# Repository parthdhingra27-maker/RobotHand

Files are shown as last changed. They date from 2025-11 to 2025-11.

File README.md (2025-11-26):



<h1 align="center">UtiliHand: A Custom Open-Source Robotic Hand</h1>
<p align="center">Project Files:</p>

<p align="center">
  <a href="https://cad.onshape.com/documents/7d4782fc1d2b81b2411dc364/w/61aa74bc50ffa663fe78e913/e/d61dc358418eba5ccd3d28ce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">Onshape CAD Files</a> •
  <a href="https://docs.google.com/spreadsheets/d/1jZwi7d67DiPdZLEvy5LfeC6HyOPPZ9pO3xaRMX1j6oo/edit?usp=sharing">Bill of Materials</a> •
  <a href="https://blueprint.hackclub.com/projects/599">Blueprint Journal</a>
</p>

I made this to robotic hand to learn more about how robotic hands are designed, built, and how they can be controlled. I also want to explore how accurate and useful they are on the end of the robotic hand I am building. This hand is designed to work using servo motors that pull string to pull the fingers down, and then elastic that pulls the fingers back upright. I learned how to design a custom PCB, encorporate an ESP32, sensors such as force sensors and flex sensors that use I2C and resistors, as well as how to make code to control servo motors.

## Features
- Simple Movement: The joints are simply 3D printed pieces with a metal rod in between that the joints rotate around.
- Cost-Effective: This robot hand with a custom PCB and all the other parts costs around $100, making it pretty cost effective.
- Off-The-Shelf-Components: This robot uses an ESP32, MG996R servo motors, fishing line, and elastic which are all easily sourceable parts.
- Wireless Control: This robot hand is powered by an ESP 32 microcontroller with has WIFI capability
- Mostly 3D Printed: This robot hand is 3D printed and doesn't require any machined parts or gearboxes.

## Design and CAD

The Onshape link can be found at the top of the README.
Each finger joint is 3d printed. A metal rod will go in each joint. The inside of the joint is press fit, and the outer parts are bigger than the rod. So the rod stays press fit, but the outer finger rotates around the rod. This is the full assembly:



This is one finger and joint:



The fishing lines pass through the palm using tunnels. the fishing line ties to the fingertip and then goes through the tunnels and ties to the servo motor. This is an example of those tunnels:



The forearm holes all the servo motors. They screw onto the forearm using heat-set inserts and M3 hardware. The forearm also includes walls that have holes for the fishing line. This is supposed to tension the fishing line. The forearm also has holes on the sides in which magnets can be inserted. This makes the top of the forearm able to close magnetically making it easier to open and close.



## PCB and Schematics:

This is the schematic for the custom PCB. The hand is powered from 24v from a bench power supply. An external buck convertor converts it into 6v since that's what the servo motors want. The main controller is an ESP32 Wroom Devkit v1. This has enough pins for all the motors and flex sensors, but an additioal ADS115 ADC Input Board is needed for additional ports for the force sensors. The PCB has JST-XH connectors for all the force and flex sensors. It has 3-pin headers for all the servo motors and screw terminals for the power input and output's. It also includes a port for I2C expansion for the future in case I add a gyroscope, etc. There is also a copper fill throughout the PCB for GND.







## Bill of Materials
These are the components needed. The prices and links can be found here:  <a href="https://docs.google.com/spreadsheets/d/1jZwi7d67DiPdZLEvy5LfeC6HyOPPZ9pO3xaRMX1j6oo/edit?usp=sharing">Bill of Materials Google Sheets</a>

- 1 x PCB
- 3D Printed Parts
- Fishing Line
- 5 x MG996R Servo Motors
- 1 x Glove
- 1 x Elastic Band
- 5 x Flex Sensors
- 5 x FSR402 Force Sensors
- 1 x ESP 32
- 1 x 45mm M4 Bolt
- 1 x 65mm M4 Bolt
- 10 x M3 Heat Set Inserts
- 4 x 6x2 Magnets
- 1 x XH-M404 Buck Convertor
- 5 x JST-XH Pigtail Wires and Connectors
- 5 x 10k Resistors
- 5 x 46k Resistors
- 1 x ADS115 ADC Board
- M3 Hardware
- 9 x JST-XH-2P
- 7 x 3 Pin Headers 2.54mm
- 1 x JST-XH 4P
- 3 x 2 Wire Screw Terminals
- 15 x 1.5mm 20mm Long Metal Rod

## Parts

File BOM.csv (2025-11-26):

Part Name | Link | Vendor | Qty | Price Per Unit | Total Item Price | Notes
Fishing Line (300M-CODE1.5-25LB) | https://www.aliexpress.us/item/3256806677560595.html?curPageLogUid=xqlwFctEmkCP | Aliexpress | 1 | $3.68 | $3.68
Elastic Band (2mm 10meters) | https://www.aliexpress.us/item/3256803466347856.html?curPageLogUid=SwbsAVxUO2GD | Aliexpress | 1 | $1.75 | $1.75
MG996R Servo Motors | https://www.aliexpress.us/item/3256807958407137.html?curPageLogUid=x0eCaFTvWNqL | Aliexpress | 5 | $3.54 | $17.70
Glove for Gesture Control | https://www.aliexpress.us/item/3256806453163489.html?curPageLogUid=y11qQYStVuEl | Aliexpress | 2 | $1.54 | $3.08 | Quantity two, one for human hand, one for robot hand to make it look professional
PCB | Screenshot | JCLPCB | 1 | $9.28 | $9.28 | Price with shipping
Flex Sensors | https://www.adafruit.com/product/1070 | Adafruit | 5 | $7.95 | $39.75 | $5 shipping for Adafruit
Force Sensors FSR402 | https://www.aliexpress.us/item/3256801705862124.html?curPageLogUid=u7hCV1u7F19a | Aliexpress | 5 | $2.11 | $10.55 | For fingertips
ESP32 | https://www.amazon.com/ESP-WROOM-32-Development-Dual-Mode-Microcontroller-Integrated/dp/B07WCG1PLV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 | Amazon | 1 | $8.99 | $8.99
M4 Bolt 45mm | https://www.aliexpress.us/item/3256805692722422.html?curPageLogUid=1TE9tD01TeyL | Aliexpress | 1 | $1.77 | $1.77 | For thumb joint
M4 Bolt 65mm | https://www.aliexpress.us/item/3256805692722422.html?curPageLogUid=1TE9tD01TeyL | Aliexpress | 1 | $2.31 | $2.31 | For ring and pinky finger joint
M3 Heat Set Inserts (4.2 OD 4mmL) | https://www.aliexpress.us/item/3256803396040989.html?curPageLogUid=uiCawpZkTW66 | Aliexpress | 1 | $2.03 | $2.03 | For Servo Motors Mounting
6x2 Magnets | https://www.aliexpress.us/item/3256809140919864.html?curPageLogUid=9g5VtP7lFqCs | Aliexpress | 1 | $3.03 | $3.03 | For mounting the top of the forearm
XH-M404 Buck Convertor | https://www.aliexpress.us/item/3256806242694144.html?curPageLogUid=DJq7uOqj9dBd | Aliexpress | 1 | $2.49 | $2.49 | Output to 6v for Servo's
JSTXH Connector and Wire | https://www.aliexpress.us/item/3256807274583113.html?curPageLogUid=7WYmVla5wsYM | Aliexpress | 2 | $1.64 | $3.28 | For sensor connectors
10k Resistors | https://www.adafruit.com/product/2784 | Adafruit | 1 | $0.75 | $0.75 | For force sensors
47k Resistors | https://www.adafruit.com/product/2786 | Adafruit | 1 | $0.75 | $0.75 | For flex sensors
ADS1115 ADC Input Board | https://www.aliexpress.us/item/3256807442377637.html?curPageLogUid=CpsMpuDdoTgi | Aliexpress | 1 | $2.40 | $2.40 | For connecting force sensors
M3 Hardware | https://www.aliexpress.us/item/3256806973435795.html?curPageLogUid=rohvX8p8T95O | Aliexpress | 1 | $8.88 | $8.88
JSTXH-2P | https://www.aliexpress.us/item/3256806894018733.html | Aliexpress | 1 | $1.60 | $1.60
3 Pin Headers | https://www.aliexpress.us/item/2255800801798474.html | Aliexpress | 1 | $1.46 | $1.46
JSTXH-4P | https://www.aliexpress.us/item/3256806894018733.html | Aliexpress | 1 | $2.33 | $2.33
2 Wire Screw Terminals | https://www.aliexpress.us/item/3256801470316663.html | Aliexpress | 1 | $1.91 | $1.91
1.5mm Metal Rod (20mm length) | https://www.aliexpress.us/item/2255800287548941.html?curPageLogUid=AwWHSz7JHJuQ | Aliexpress | 1 | $1.99 | $1.99 | To connect each joint together
Parts Total | $131.76
Shipping Total | $5.00 | Adafruit Shipping
Subtotal | $136.76
Tax (Virginia 4.5%) | $6.15
Project Total | $142.91

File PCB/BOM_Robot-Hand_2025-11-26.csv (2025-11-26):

ID | Name | Designator | Footprint | Quantity | Manufacturer Part | Manufacturer | Supplier | Supplier Part | Price
1 | CAP0805_0.1uF_100V | 0.1UFCAPACITOR | CAP0805 | 1 |  | TDK Corporation
2 | 47k | 1FLEX47K,2FLEX27K,3FLEX47K,4FLEX47K,5FLEX47K | R_AXIAL_DIN0207_L6.3MM_D2.5MM_P7.62MM_HORIZONTAL | 5
3 | 10k | 1FORCE10K,2FORCE10K,3FORCE10K,4FORCE10K | R_AXIAL_DIN0207_L6.3MM_D2.5MM_P7.62MM_HORIZONTAL | 4
4 | XY301V-A-5.0-2P 2 PIN TERMINAL BLOCK | 6VBUCK,24VTOBUCK | CONN-TH_XY301V-A-5.0-2P | 2 | XY301V-A-5.0-2P | XINLAIYA(新莱亚) | LCSC | C557651 | 0.105
5 | KF301-2P | 24VINPUT | CONN-TH_XY301V-A-5.0-2P | 1 | KF301-2P接线端子 | null | LCSC | C9900016950
6 | ADAFRUIT_ADS1115_16BIT | ADS1115 | PCB ADS115 | 1
7 | XH-2_54-2P | FLEX1,FLEX2,FLEX3,FLEX4,FLEX5,FORCE1,FORCE2,FORCE3,FORCE4 | CONN-TH_XH-2_54-2P | 9 | XH-2_54-2P | null | LCSC | C9900011447
8 | JST-XHP-4-PIN | I2C | JST-XHP-4-PIN | 1
9 | KIP_DIODE_SMABF_M7_SS54 | INPUTDIODE | KIP_DIODE_SMABF_M7_SS54 | 1 | 1N4007G | SK | LCSC | C111122 | 0.014
10 | MF-R300 | INPUTFUSE | FUSE-TH_L12.8-W3.0-P5.80-D1.2-S2.20 | 1 | MF-R300 | BOURNS | LCSC | C208487 | 0.257
11 | LED | LED1 | LED-TH_LED-DP2-2LED-AMCC | 1 | 5600 | VccLite | Digi-Key | L20325-ND
12 | Resistor_220Ohm | LEDRESISTOR1 | RESISTOR_220OHM | 1
13 | ESP32-DEVKITV1_REAL_SIZE | MAINBOARD1 | ESP32-DEVKITV1_ESP32-DEVKITV1 | 1
14 | 2.54MM_1*3_PIN | SERVO1,SERVO2,SERVO3,SERVO4,SERVO5,SERVO6,SERVO7 | 2.54MM:PINHEADER_1X3_P_2.54MM | 7 | Female headerHDR1X8-2.54 | BOOMELE | LCSC | C27438 | 0.078

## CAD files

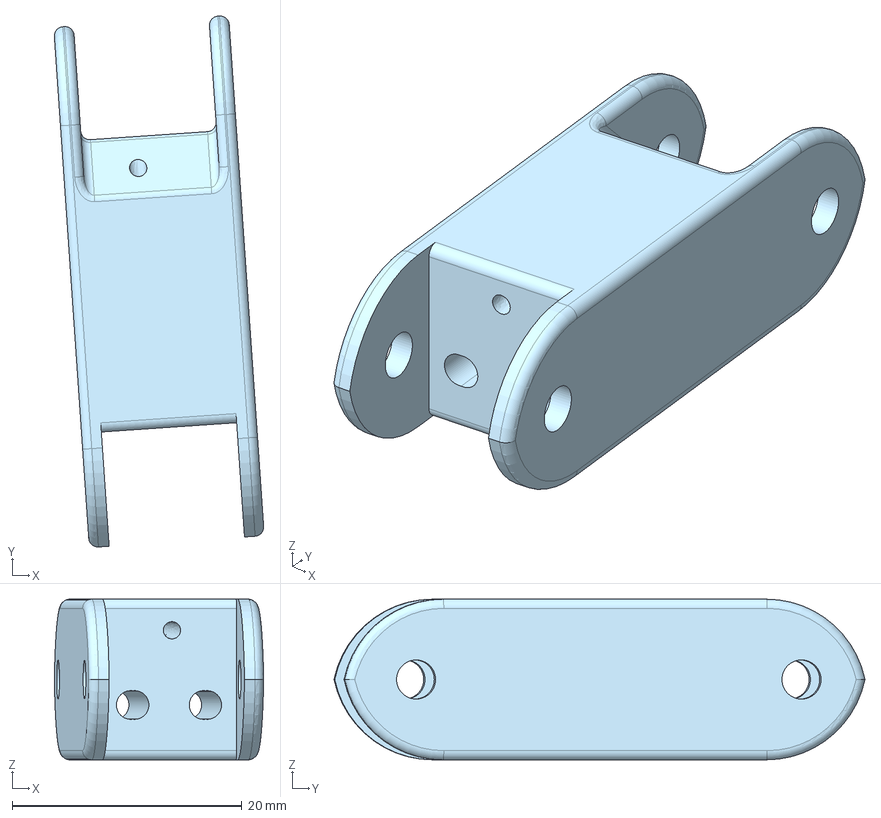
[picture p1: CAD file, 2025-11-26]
CAD/MAIN SKETCH - Pinky2.step
18.2 x 46.2 x 14.0 mm

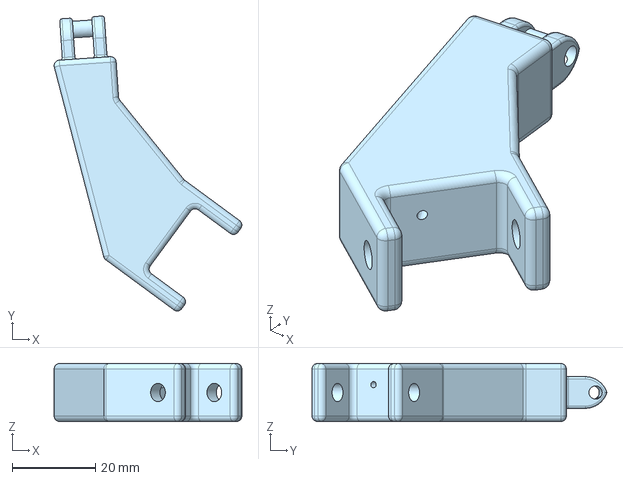
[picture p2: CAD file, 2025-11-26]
CAD/MAIN SKETCH - Pinky1.step
45.2 x 71.0 x 14.0 mm

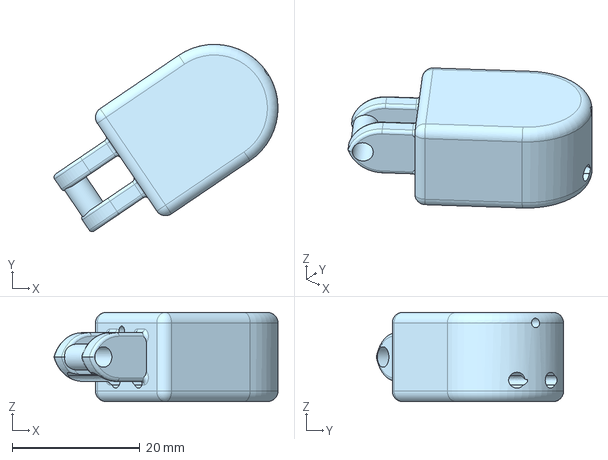
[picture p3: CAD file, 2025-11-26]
CAD/MAIN SKETCH - Thumb3.step
35.0 x 29.3 x 14.0 mm

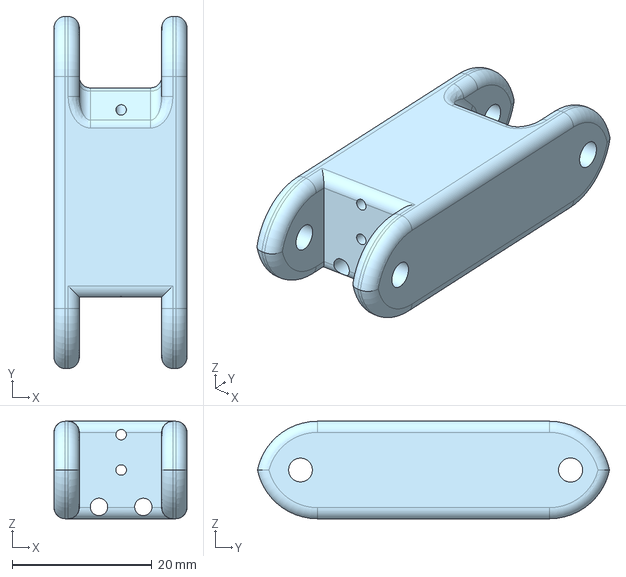
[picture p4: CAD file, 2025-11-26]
CAD/MAIN SKETCH - Middle1.step
19.0 x 50.4 x 14.0 mm

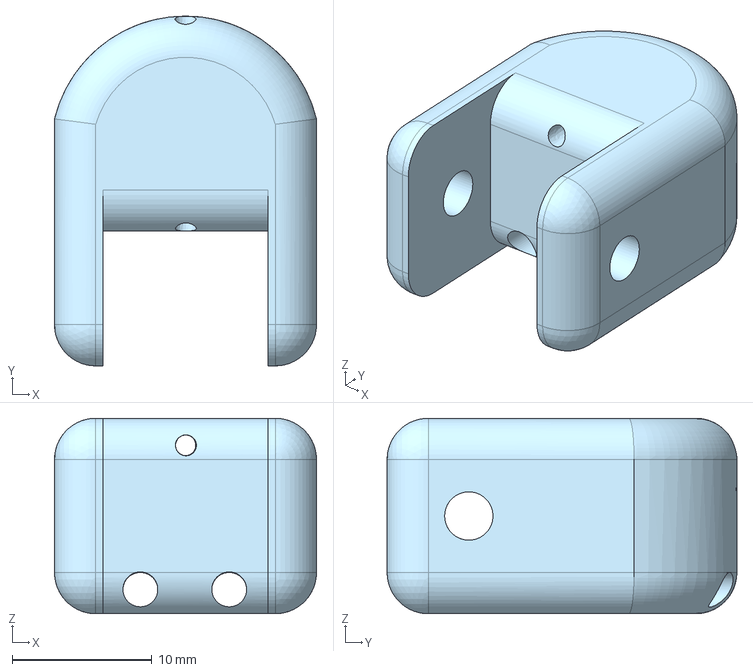
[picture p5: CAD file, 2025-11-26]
CAD/MAIN SKETCH - Ring4.step
18.7 x 25.0 x 14.0 mm

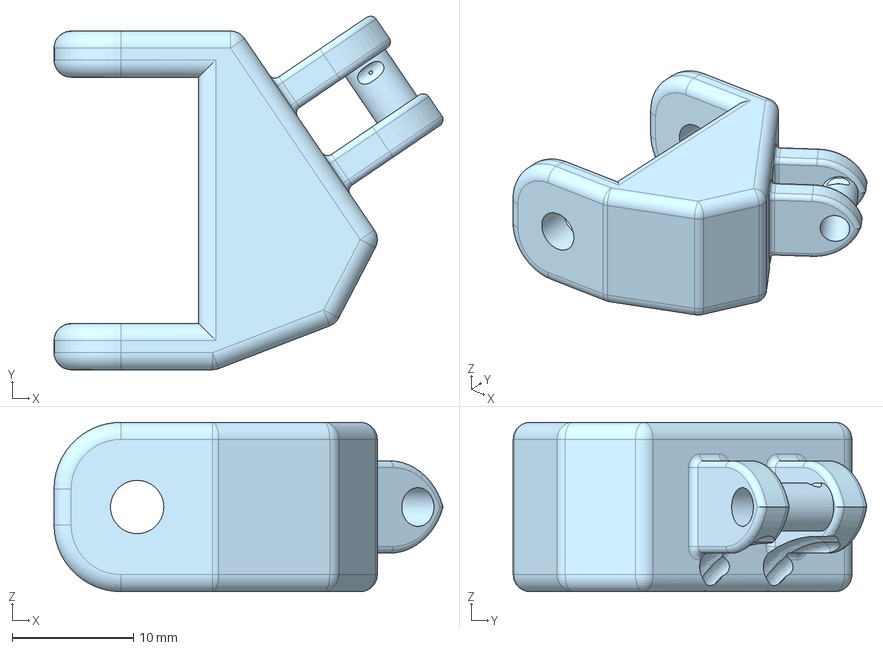
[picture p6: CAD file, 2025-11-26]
CAD/MAIN SKETCH - Thumb1.step
32.1 x 29.2 x 14.0 mm

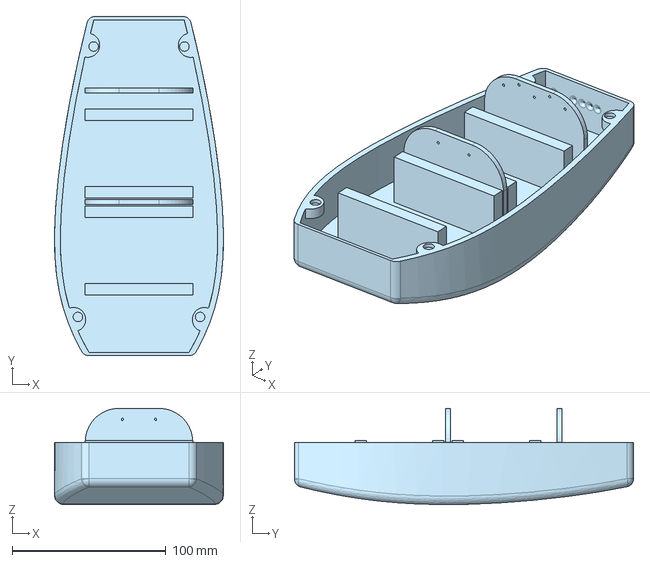
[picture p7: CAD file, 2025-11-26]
CAD/MAIN SKETCH - FOREARM (1).step
110.0 x 220.7 x 62.6 mm

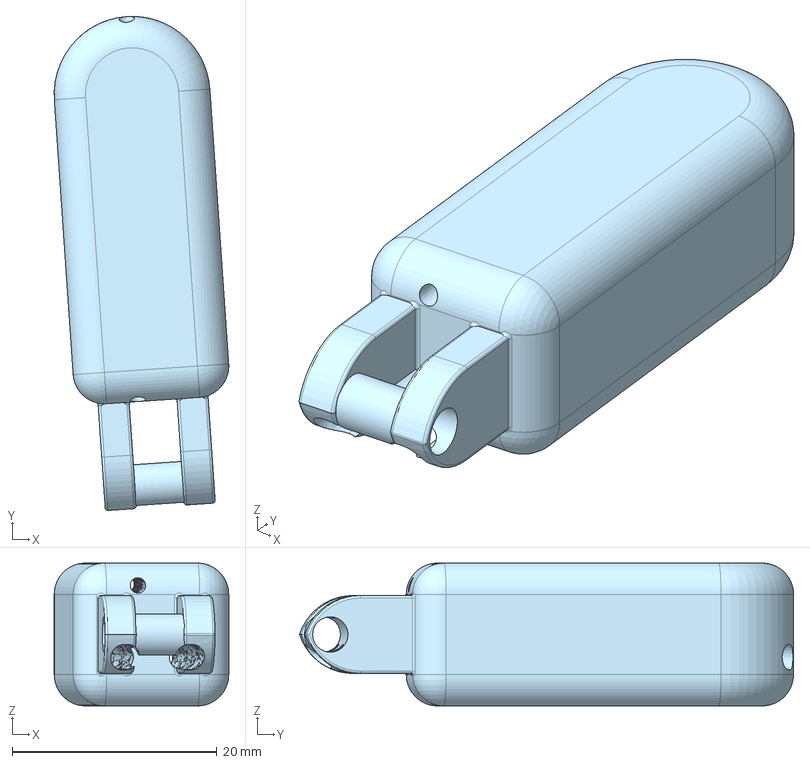
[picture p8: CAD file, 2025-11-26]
CAD/MAIN SKETCH - Pinky3.step
17.1 x 48.3 x 14.0 mm

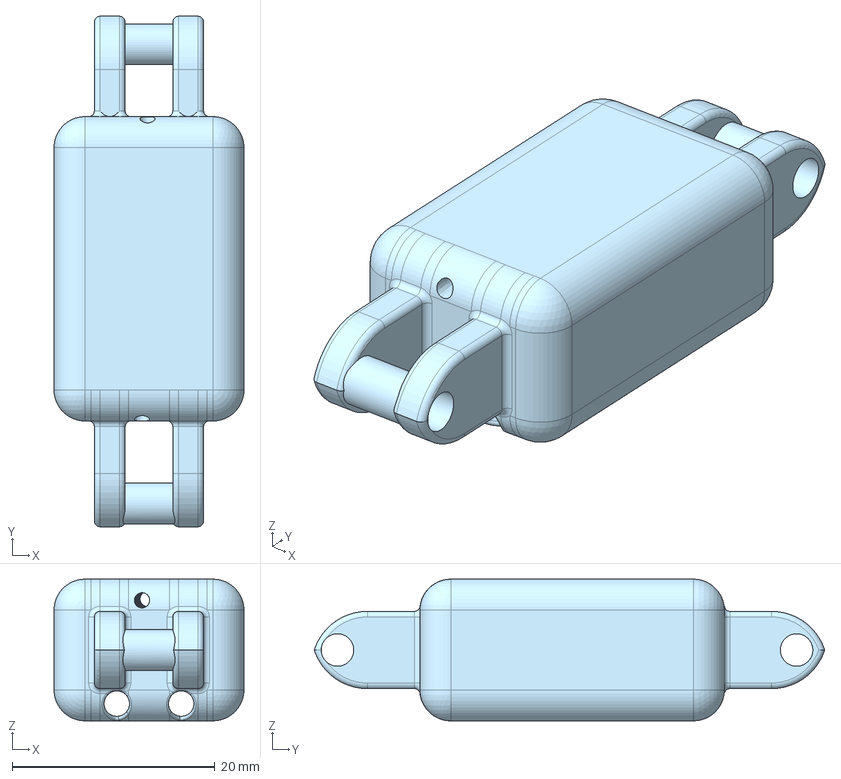
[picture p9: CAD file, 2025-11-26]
CAD/MAIN SKETCH - Index2.step
18.7 x 50.3 x 14.0 mm

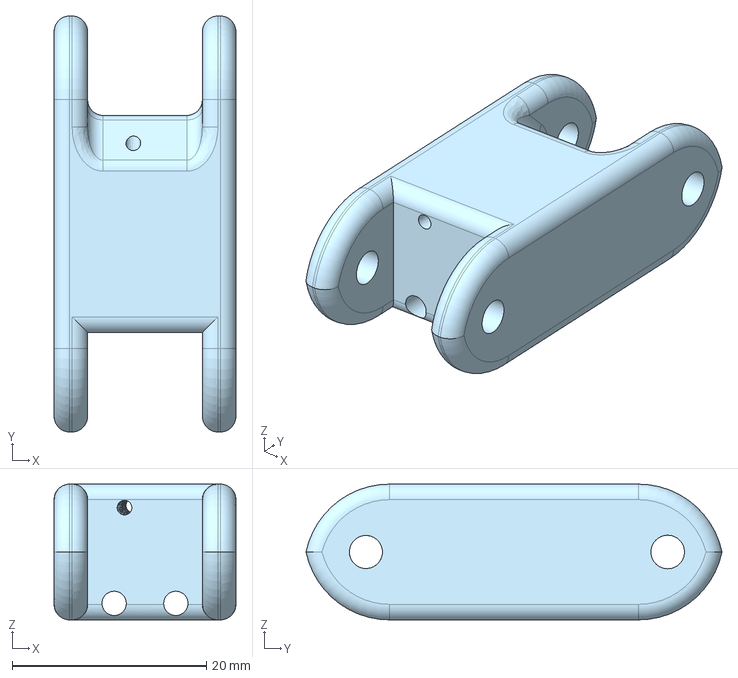
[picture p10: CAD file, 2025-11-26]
CAD/MAIN SKETCH - Index1.step
18.7 x 42.8 x 14.0 mm

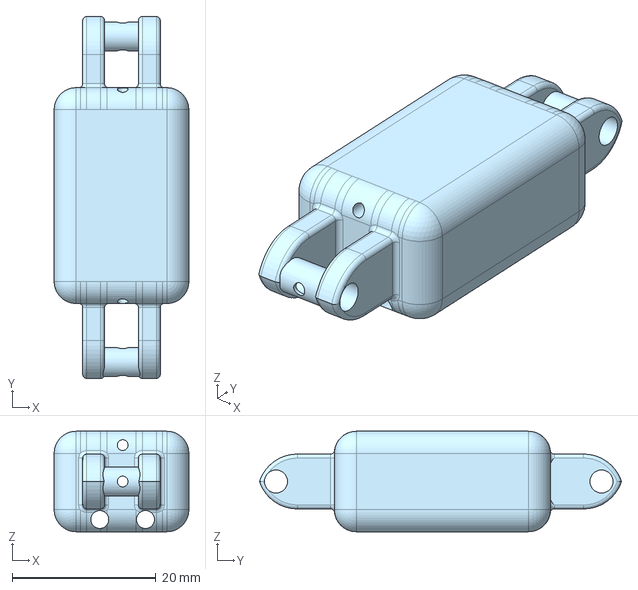
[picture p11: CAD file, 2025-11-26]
CAD/MAIN SKETCH - Middle2.step
18.7 x 50.3 x 14.0 mm

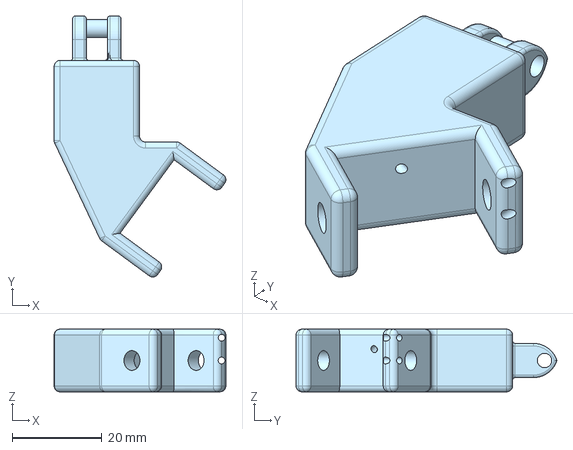
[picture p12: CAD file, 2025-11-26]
CAD/MAIN SKETCH - Ring1.step
38.3 x 58.2 x 14.0 mm

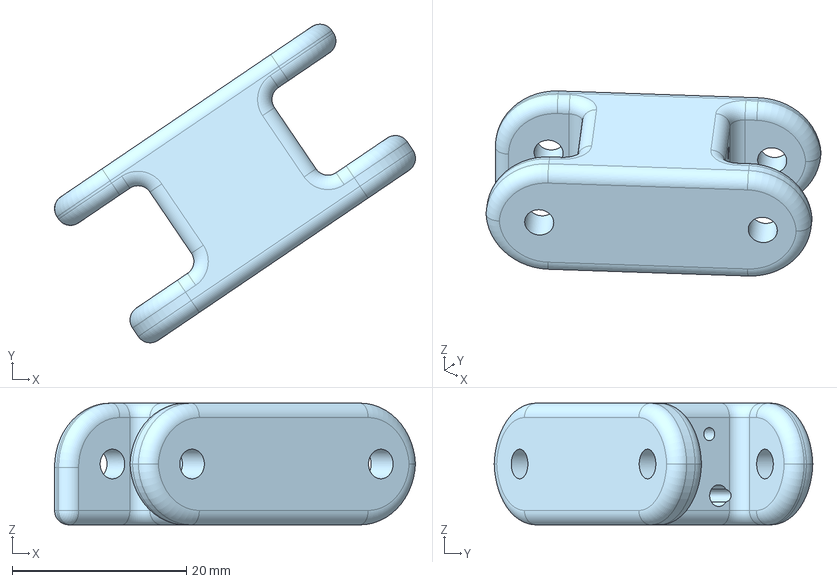
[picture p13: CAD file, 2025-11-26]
CAD/MAIN SKETCH - Thumb2.step
41.4 x 36.5 x 14.0 mm

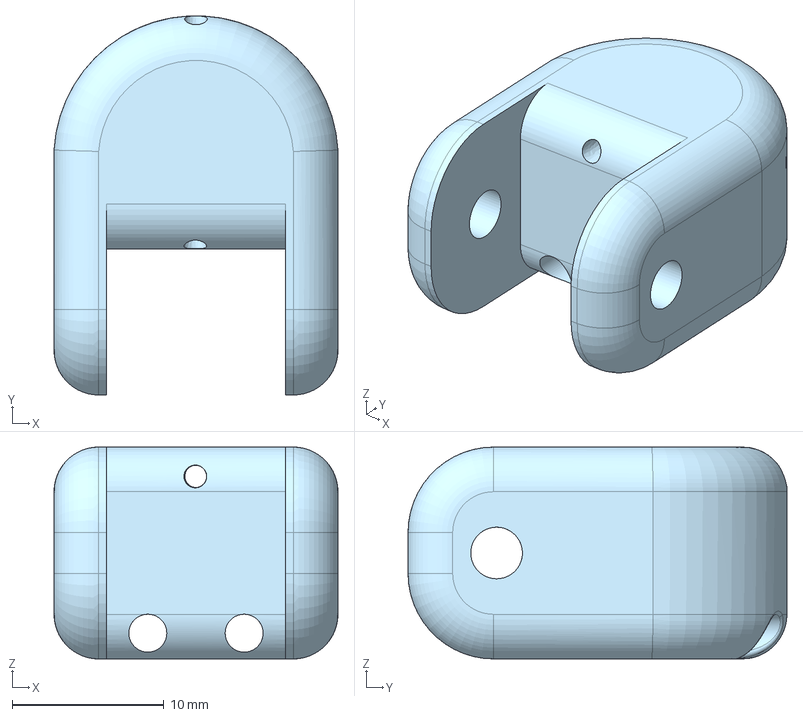
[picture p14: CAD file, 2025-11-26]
CAD/MAIN SKETCH - Index3.step
18.7 x 25.0 x 14.0 mm

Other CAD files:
CAD/MAIN SKETCH - Middle3.step
CAD/MAIN SKETCH - Ring3.step
CAD/MAIN SKETCH - Ring2.step
CAD/MAIN SKETCH - Palm.step
CAD/Assembly 1.step

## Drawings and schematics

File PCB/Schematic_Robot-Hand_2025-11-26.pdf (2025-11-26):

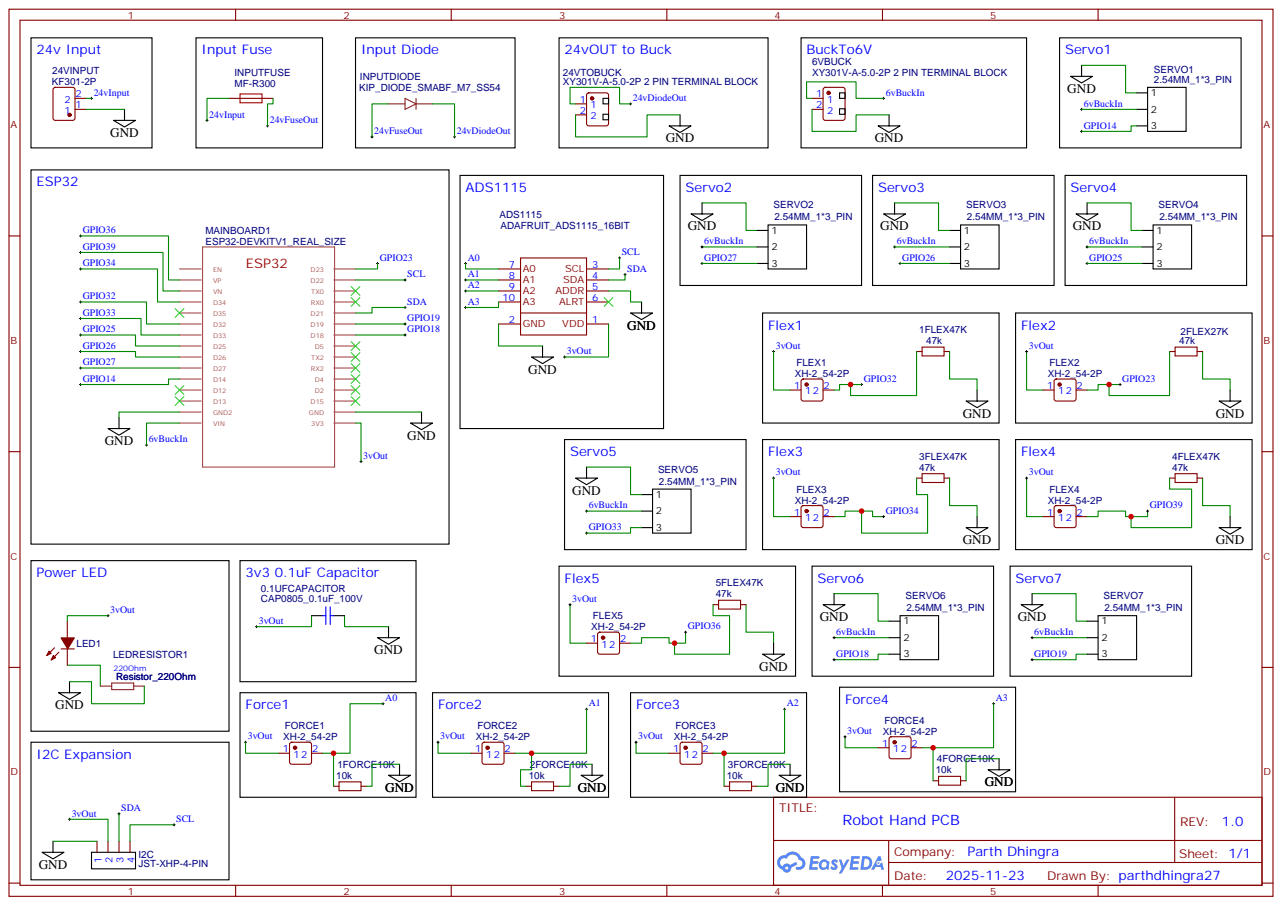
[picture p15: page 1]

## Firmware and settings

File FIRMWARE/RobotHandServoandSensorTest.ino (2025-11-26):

#include <Wire.h>
#include <Servo.h>

// ----- ADS1115 Address -----
#define ADS_ADDR 0x48   // Default address

// ----- Servo Objects -----
Servo servo1;
Servo servo2;
Servo servo3;
Servo servo4;

// ----- Pin Assignments -----
int servoPin1 = 13;
int servoPin2 = 12;
int servoPin3 = 14;
int servoPin4 = 27;

// ----- Basic Setup -----
void setup() {
  Serial.begin(115200);

  // I2C init
  Wire.begin(21, 22);   // SDA = 21, SCL = 22

  // Servos
  servo1.attach(servoPin1);
  servo2.attach(servoPin2);
  servo3.attach(servoPin3);
  servo4.attach(servoPin4);

  Serial.println("Robot Hand Firmware Started");
}

// ----- Read From ADS1115 -----
int16_t readADS(int channel) {
  // Select channel
  uint16_t config = 0x8400; // Single-ended AIN0
  if(channel == 1) config = 0x9400; // AIN1
  if(channel == 2) config = 0xA400; // AIN2
  if(channel == 3) config = 0xB400; // AIN3

  // Always add fixed bits
  config |= 0x8000;  // Start single conversion
  config |= 0x0183;  // 4.096V range, 128SPS

  Wire.beginTransmission(ADS_ADDR);
  Wire.write(0x01);                   // Config register
  Wire.write(config >> 8);
  Wire.write(config & 0xFF);
  Wire.endTransmission();

  delay(8); // ADS1115 conversion time

  Wire.beginTransmission(ADS_ADDR);
  Wire.write(0x00);                   // Conversion register
  Wire.endTransmission();

  Wire.requestFrom(ADS_ADDR, 2);
  int16_t result = (Wire.read() << 8) | Wire.read();
  return result;
}

// ----- Map Flex → Servo -----
int mapFlexToAngle(int16_t v) {
  // You will tune these
  int minV = 12000;
  int maxV = 24000;

  v = constrain(v, minV, maxV);
  return map(v, minV, maxV, 0, 180);
}

// ----- MAIN LOOP -----
void loop() {
  int s1 = mapFlexToAngle(readADS(0));
  int s2 = mapFlexToAngle(readADS(1));
  int s3 = mapFlexToAngle(readADS(2));
  int s4 = mapFlexToAngle(readADS(3));

  servo1.write(s1);
  servo2.write(s2);
  servo3.write(s3);
  servo4.write(s4);

  // Debug output
  Serial.print("S1: "); Serial.print(s1);
  Serial.print("  S2: "); Serial.print(s2);
  Serial.print("  S3: "); Serial.print(s3);
  Serial.print("  S4: "); Serial.println(s4);

  delay(10);
}
